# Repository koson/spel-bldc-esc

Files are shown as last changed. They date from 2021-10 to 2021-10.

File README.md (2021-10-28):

# SPEL electronic speed controller for BLDC motors 

Open-source hardware and software for BLDC motor electronic speed controller.

### About
Yet another open-source BLDC motor controller, developed primarily as a learning project. 

The end-goal is to create a controller that would be compact, flexibla and cheap to manufacture (design rules compliant with the ones from JLCPCB - 
same goes for most of the electronic components available at their SMD/SMT parts library). 

### Specification:
- Rated voltage: 60 [VDC]
- Rated current: 60 [ADC]
- Communication interfaces: CAN, I2C, UART, USB
- Debugging interface: SWD
- Control methods: through comm. interfaces, STEP/DIRECTION
- Feedback: Encoder inputs (reprogrammable to HAL sensor inputs), current sensing, back-EMF measurement. 
- CPU: STM32F103C8Tx/STM32F103CBTx series 
- Motor driver: Texas Instrument's DRV8301 
- Protection: DRV8301's built-in overcurrent/overvoltage protection modules, braking resistor.



### Hardware renders 


*SWD - IRL would be a pin header, not a socket, 3D model used for a footprint that happened to fit pin numeration accurately





### TODO: 
- BOM
- Manufacturing outlines (listing cheapest options, and possible part substitutes)
- Append calculations (somewhere)

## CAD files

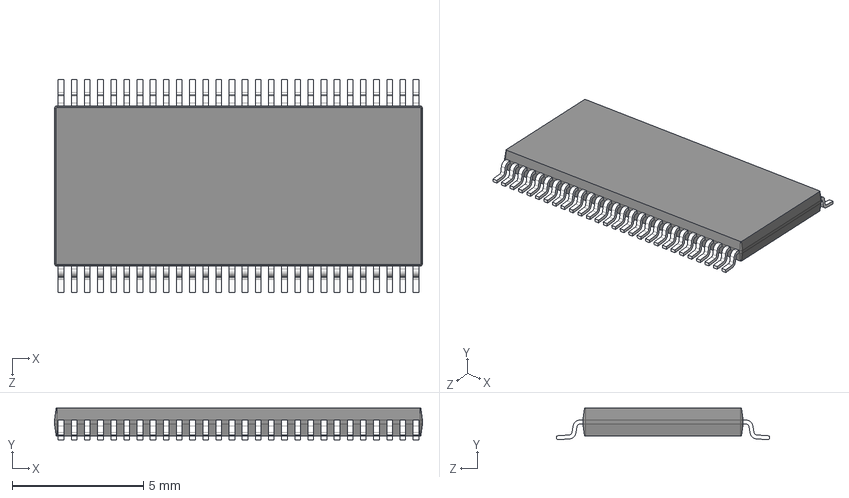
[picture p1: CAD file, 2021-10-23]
hardware/component_models/DRV8301DCAR.step
14.0 x 1.20 x 8.10 mm

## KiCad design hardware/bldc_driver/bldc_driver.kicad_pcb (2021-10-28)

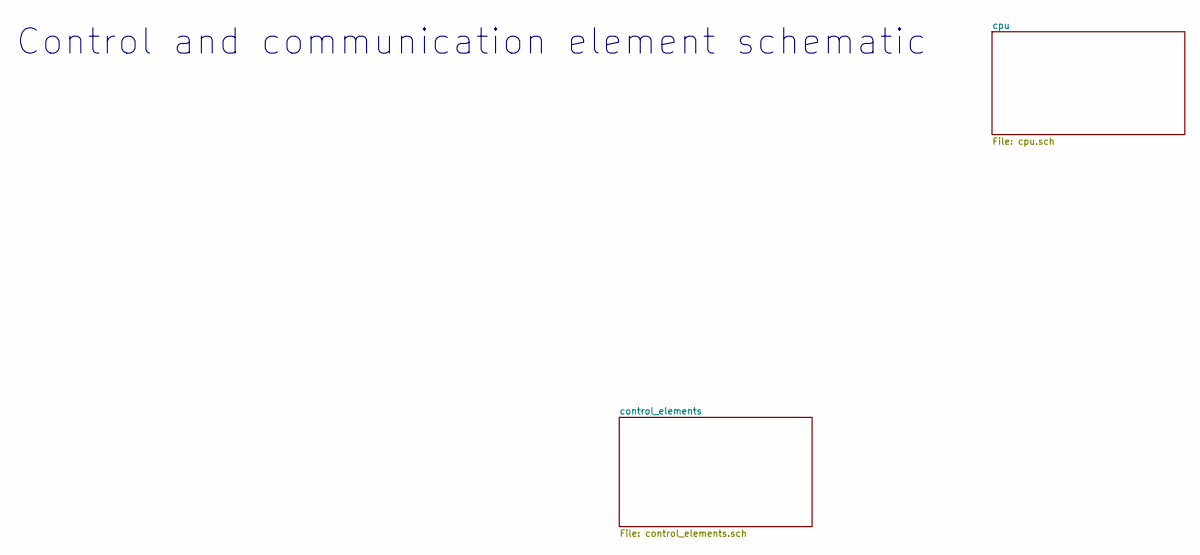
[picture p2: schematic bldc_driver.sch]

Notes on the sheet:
Control and communication element schematic

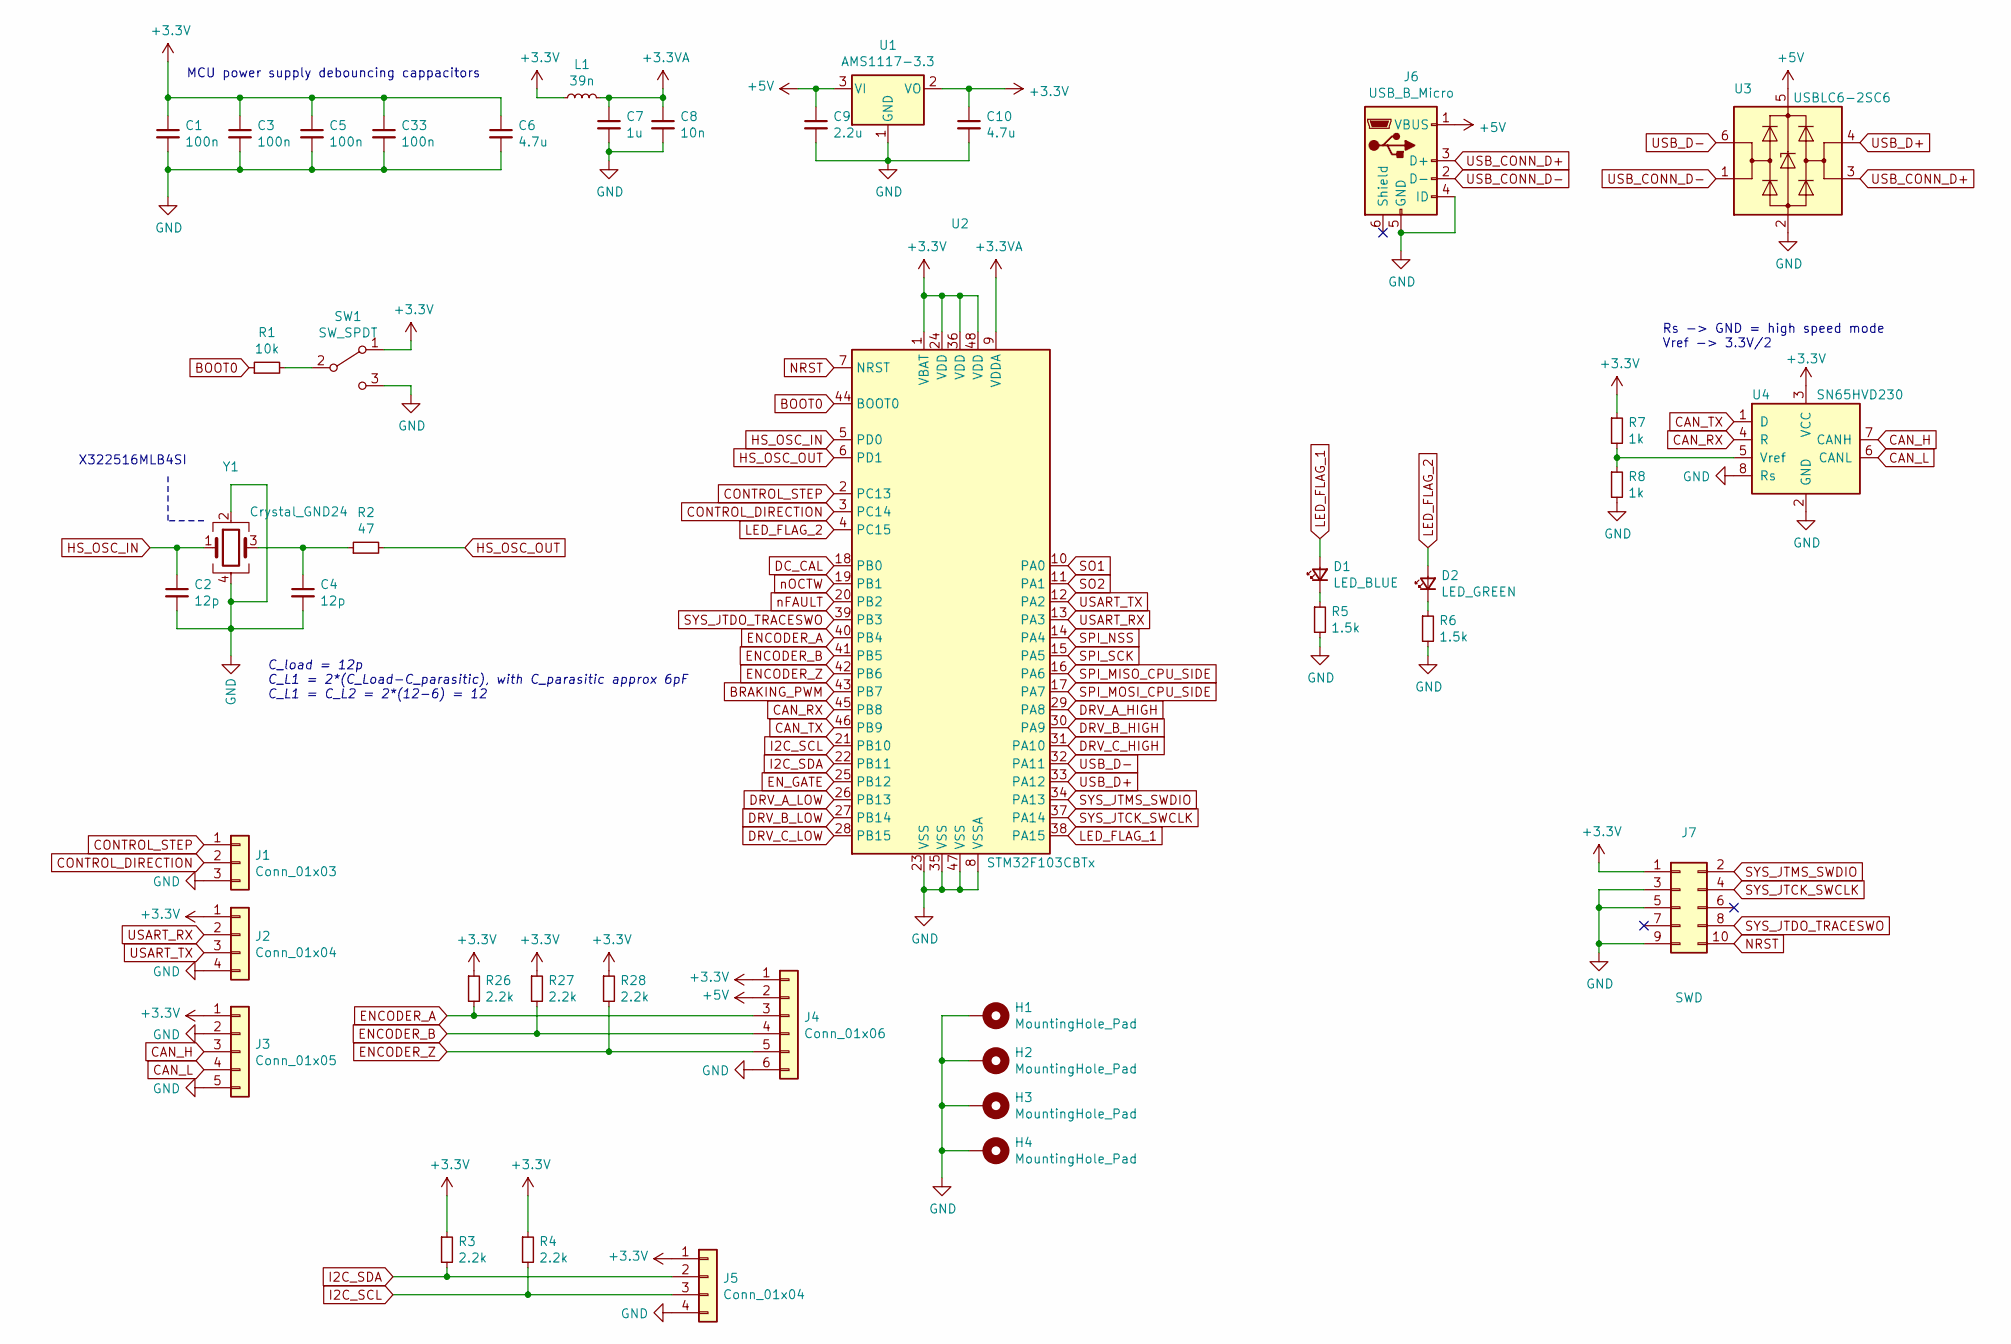
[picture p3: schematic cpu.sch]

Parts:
C1, C3, C5, C33: 100n; C_0402_1005Metric
C2, C4: 12p; C_0402_1005Metric
C6: 4.7u; C_0402_1005Metric
C7: 1u; C_0805_2012Metric
C8: 10n; C_0805_2012Metric
C9: 2.2u; C_0805_2012Metric
C10: 4.7u; C_0805_2012Metric
D1: LED_BLUE; LED_0603_1608Metric
D2: LED_GREEN; LED_0603_1608Metric
H1, H2, H3, H4: MountingHole_Pad; MountingHole_4.3mm_M4_Pad_Via
J1: Conn_01x03; PinSocket_1x03_P2.54mm_Vertical
J2, J5: Conn_01x04; PinSocket_1x04_P2.54mm_Vertical
J3: Conn_01x05; PinSocket_1x05_P2.54mm_Vertical
J4: Conn_01x06; PinSocket_1x06_P2.54mm_Vertical
J6: USB_B_Micro; USB_Micro-B_Molex_47346-0001
J7: SWD; PinSocket_2x05_P1.27mm_Vertical_SMD
L1: 39n; L_0402_1005Metric
R1: 10k; R_0402_1005Metric
R2: 47; R_0402_1005Metric
R3, R4, R26, R27, R28: 2.2k; R_0603_1608Metric
R5, R6: 1.5k; R_0603_1608Metric
R7, R8: 1k; R_0603_1608Metric
SW1: SW_SPDT; SW_SPDT_PCM12
U1: AMS1117-3.3; SOT-223-3_TabPin2
U2: STM32F103CBTx; LQFP-48_7x7mm_P0.5mm
U3: USBLC6-2SC6; SOT-23-6
U4: SN65HVD230; SOIC-8_3.9x4.9mm_P1.27mm
Y1: Crystal_GND24; Crystal_SMD_3225-4Pin_3.2x2.5mm

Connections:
+3.3VA: C7.1, C8.1, L1.2, U2.9 (VDDA); also elsewhere on the board
+3V3: C1.1, C3.1, C5.1, C6.1, C10.1, C33.1, J2.1, J3.1, J4.1, J5.1, J7.1, L1.1, R3.1, R4.1, R7.1, R26.1, R27.1, R28.1, SW1.1 (A), U1.2 (VO), U2.1 (VBAT), U2.24 (VDD), U2.36 (VDD), U2.48 (VDD), U4.3 (VCC); also elsewhere on the board
+5V: C9.1, J4.2, J6.1 (VBUS), U1.3 (VI), U3.5 (VBUS); also elsewhere on the board
-VDC: C1.2, C2.2, C3.2, C4.2, C5.2, C6.2, C7.2, C8.2, C9.2, C10.2, C33.2, H1.1, H2.1, H3.1, H4.1, J1.3, J2.4, J3.2, J3.5, J4.6, J5.4, J6.4 (ID), J6.5 (GND), J7.3, J7.5, J7.9, R5.2, R6.2, R8.2, SW1.3 (C), U1.1 (GND), U2.8 (VSSA), U2.23 (VSS), U2.35 (VSS), U2.47 (VSS), U3.2 (GND), U4.2 (GND), U4.8 (Rs), Y1.2, Y1.4; also elsewhere on the board
BOOT0: R1.1, U2.44 (BOOT0)
BRAKING_PWM: U2.43 (PB7); also elsewhere on the board
CAN_H: J3.3, U4.7 (CANH)
CAN_L: J3.4, U4.6 (CANL)
CAN_RX: U2.45 (PB8), U4.4 (R)
CAN_TX: U2.46 (PB9), U4.1 (D)
CONTROL_DIRECTION: J1.2, U2.3 (PC14)
CONTROL_STEP: J1.1, U2.2 (PC13)
DC_CAL: U2.18 (PB0); also elsewhere on the board
DRV_A_HIGH: U2.29 (PA8); also elsewhere on the board
DRV_A_LOW: U2.26 (PB13); also elsewhere on the board
DRV_B_HIGH: U2.30 (PA9); also elsewhere on the board
DRV_B_LOW: U2.27 (PB14); also elsewhere on the board
DRV_C_HIGH: U2.31 (PA10); also elsewhere on the board
DRV_C_LOW: U2.28 (PB15); also elsewhere on the board
ENCODER_A: J4.3, R26.2, U2.40 (PB4)
ENCODER_B: J4.4, R27.2, U2.41 (PB5)
ENCODER_Z: J4.5, R28.2, U2.42 (PB6)
EN_GATE: U2.25 (PB12); also elsewhere on the board
HS_OSC_IN: C2.1, U2.5 (PD0), Y1.1
HS_OSC_OUT: R2.2, U2.6 (PD1)
I2C_SCL: J5.3, R4.2, U2.21 (PB10)
I2C_SDA: J5.2, R3.2, U2.22 (PB11)
LED_FLAG_1: D1.2 (A), U2.38 (PA15)
LED_FLAG_2: D2.2 (A), U2.4 (PC15)
NRST: J7.10, U2.7 (NRST)
unnamed: C4.1, R2.1, Y1.3
unnamed: D1.1 (K), R5.1
unnamed: D2.1 (K), R6.1
unnamed: R1.2, SW1.2 (B)
unnamed: R7.2, R8.1, U4.5 (Vref)
SO1: U2.10 (PA0); also elsewhere on the board
SO2: U2.11 (PA1); also elsewhere on the board
SPI_MISO_CPU_SIDE: U2.16 (PA6); also elsewhere on the board
SPI_MOSI_CPU_SIDE: U2.17 (PA7); also elsewhere on the board
SPI_NSS: U2.14 (PA4); also elsewhere on the board
SPI_SCK: U2.15 (PA5); also elsewhere on the board
SYS_JTCK_SWCLK: J7.4, U2.37 (PA14)
SYS_JTDO_TRACESWO: J7.8, U2.39 (PB3)
SYS_JTMS_SWDIO: J7.2, U2.34 (PA13)
USART_RX: J2.2, U2.13 (PA3)
USART_TX: J2.3, U2.12 (PA2)
USB_CONN_D+: J6.3 (D+), U3.3 (I/O2)
USB_CONN_D-: J6.2 (D-), U3.1 (I/O1)
USB_D+: U2.33 (PA12), U3.4 (I/O2)
USB_D-: U2.32 (PA11), U3.6 (I/O1)
nFAULT: U2.20 (PB2); also elsewhere on the board
nOCTW: U2.19 (PB1); also elsewhere on the board

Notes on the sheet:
C_load = 12p C_L1 = 2*(C_Load-C_parasitic), with C_parasitic approx 6pF C_L1 = C_L2 = 2*(12-6) = 12
Rs -> GND = high speed mode Vref -> 3.3V/2
X322516MLB4SI
MCU power supply debouncing cappacitors

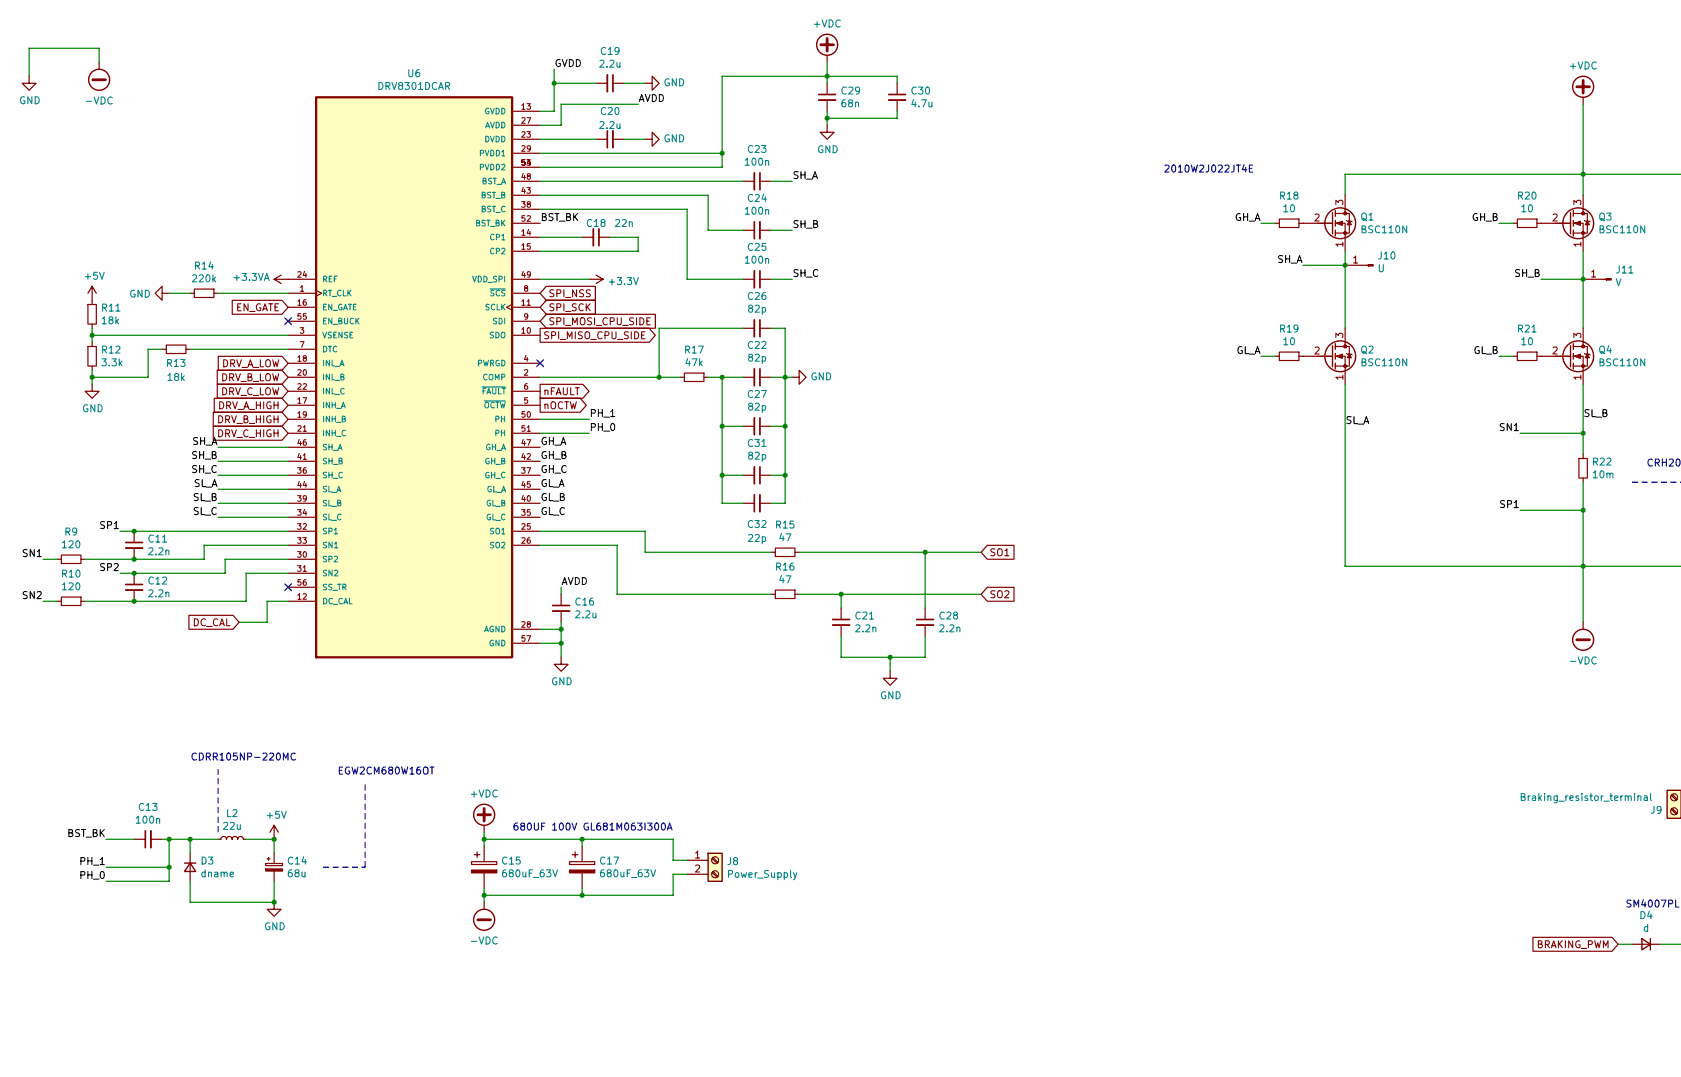
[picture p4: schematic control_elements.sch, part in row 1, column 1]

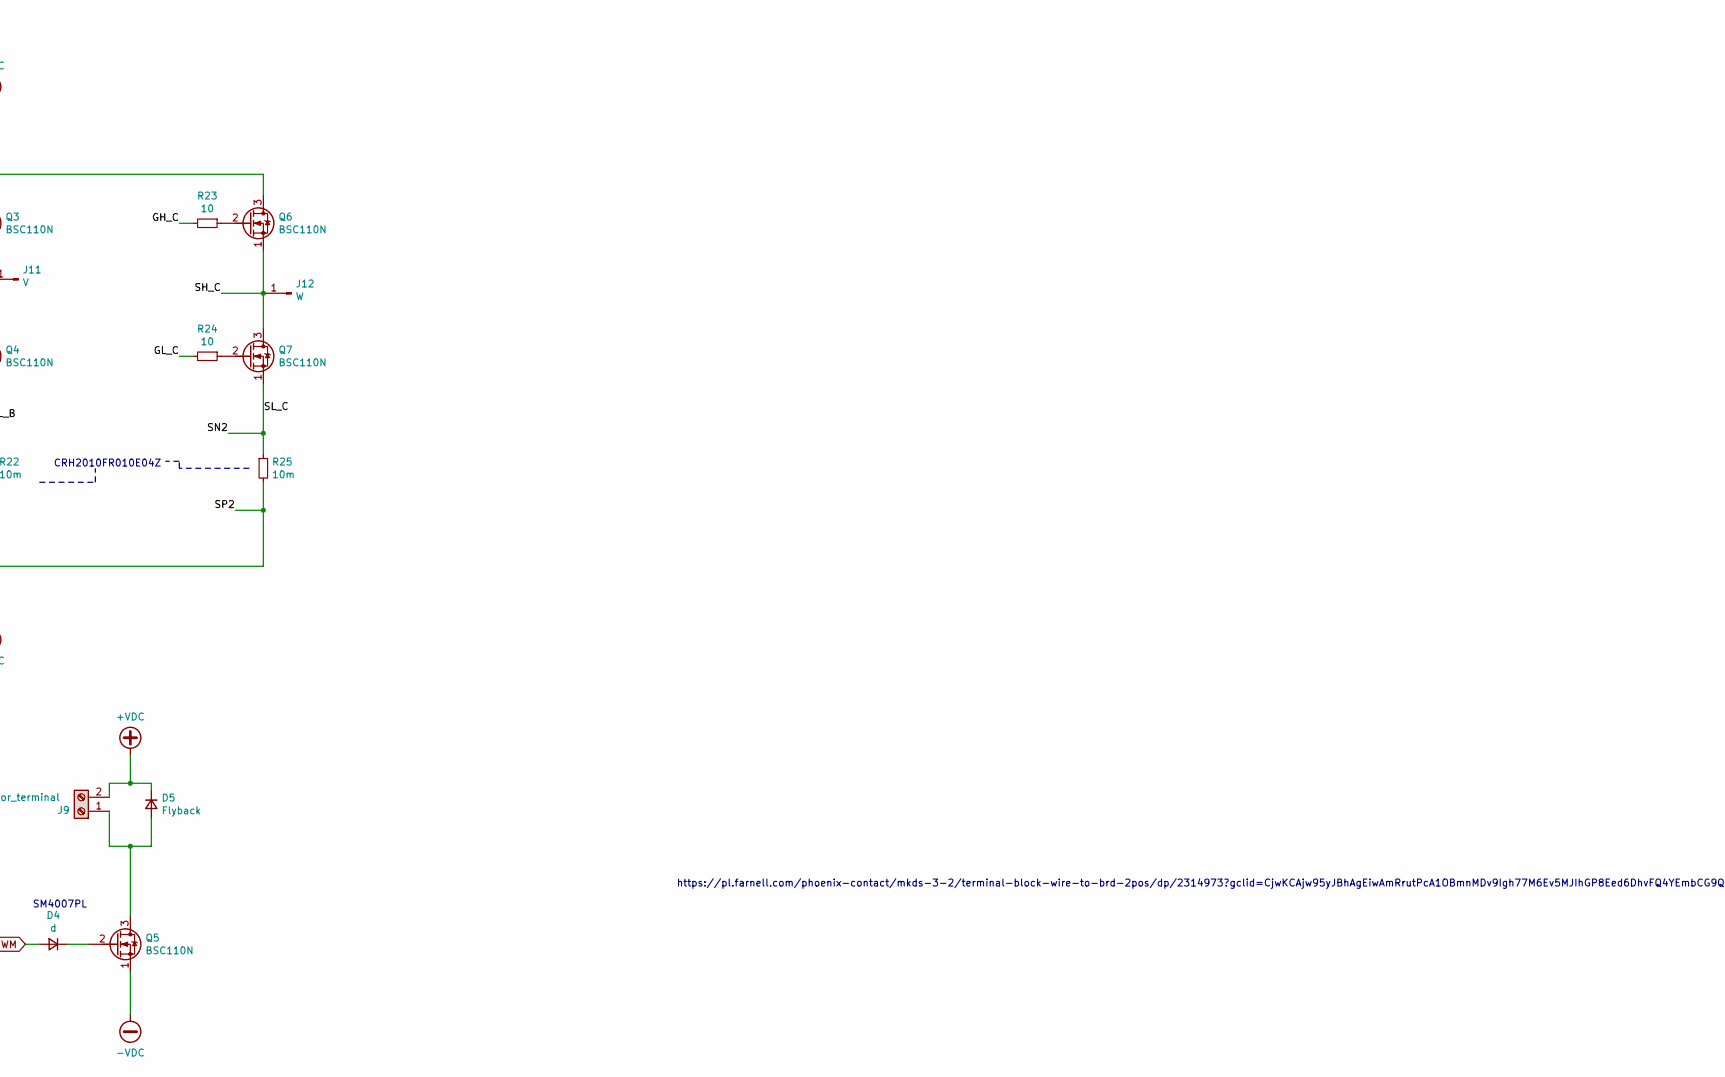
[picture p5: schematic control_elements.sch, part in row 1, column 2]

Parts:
C11, C12, C21, C28: 2.2n; C_0805_2012Metric
C13, C23, C24, C25: 100n; C_0805_2012Metric
C14: 68u; CP_Radial_D12.5mm_P5.00mm
C15, C17: 680uF_63V; CP_Radial_D13.0mm_P5.00mm
C16, C19, C20: 2.2u; C_0805_2012Metric
C18: 22n; C_0805_2012Metric
C22, C26, C27, C31: 82p; C_0603_1608Metric
C29: 68n; C_Rect_L10.0mm_W5.0mm_P5.00mm_P7.50mm
C30: 4.7u; C_1210_3225Metric
C32: 22p; C_0603_1608Metric
D3: dname; D_SOD-123F
D4: d; D_SOD-123F
D5: Flyback; D_SOD-123F
J8: Power_Supply; AMASS_XT60-F_1x02_P7.20mm_Vertical
J9: Braking_resistor_terminal; TerminalBlock_Phoenix_MKDS-3-2-5.08_1x02_P5.08mm_Horizontal
J10: U; motor_driving_pad_hole
J11: V; motor_driving_pad_hole
J12: W; motor_driving_pad_hole
L2: 22u; L_10.4x10.4_H4.8
Q1, Q2, Q3, Q4, Q5, Q6, Q7: BSC110N
R9, R10: 120; R_0805_2012Metric
R11, R13: 18k; R_0603_1608Metric
R12: 3.3k; R_0603_1608Metric
R14: 220k; R_0603_1608Metric
R15, R16: 47; R_0402_1005Metric
R17: 47k; R_0603_1608Metric
R18, R19, R20, R21, R23, R24: 10; R_0402_1005Metric
R22, R25: 10m; R_2010_5025Metric
U6: DRV8301DCAR; HTSSOP-56-1EP_6.1x14mm_P0.5mm_EP3.61x6.35mm; PARTREV F

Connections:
+3.3VA: U6.24 (REF); also elsewhere on the board
+3V3: U6.49 (VDD_SPI); also elsewhere on the board
+5V: C14.1, L2.2, R11.1; also elsewhere on the board
+VDC: C15.1, C17.1, C29.1, C30.1, D5.1 (K), J8.1, J9.2, Q1.3 (D), Q3.3 (D), Q6.3 (D), U6.29 (PVDD1), U6.53 (PVDD2), U6.54 (PVDD2)
-VDC: C11.1, C12.1, C14.2, C15.2, C16.2, C17.2, C19.1, C20.2, C21.2, C22.1, C26.1, C27.1, C28.2, C29.2, C30.2, C31.1, C32.2, D3.2 (A), J8.2, Q2.1 (S), Q5.1 (S), R12.2, R13.1, R14.2, R22.2, R25.2, U6.28 (AGND), U6.30 (SP2), U6.32 (SP1), U6.44 (SL_A), U6.57 (GND); also elsewhere on the board
/control_elements/AVDD: C16.1, U6.27 (AVDD)
/control_elements/BST_BK: C13.1, U6.52 (BST_BK)
/control_elements/GH_A: R18.2, U6.47 (GH_A)
/control_elements/GH_B: R20.2, U6.42 (GH_B)
/control_elements/GH_C: R23.2, U6.37 (GH_C)
/control_elements/GL_A: R19.2, U6.45 (GL_A)
/control_elements/GL_B: R21.2, U6.40 (GL_B)
/control_elements/GL_C: R24.2, U6.35 (GL_C)
/control_elements/GVDD: C19.2, U6.13 (GVDD)
/control_elements/PH_0: C13.2, D3.1 (K), L2.1, U6.50 (PH), U6.51 (PH)
/control_elements/SH_A: C23.1, J10.1, Q1.1 (S), Q2.3 (D), U6.46 (SH_A)
/control_elements/SH_B: C24.2, J11.1, Q3.1 (S), Q4.3 (D), U6.41 (SH_B)
/control_elements/SH_C: C25.1, J12.1, Q6.1 (S), Q7.3 (D), U6.36 (SH_C)
/control_elements/SL_B: Q4.1 (S), R9.1, R22.1, U6.39 (SL_B)
/control_elements/SL_C: Q7.1 (S), R10.2, R25.1, U6.34 (SL_C)
BRAKING_PWM: D4.2 (A); also elsewhere on the board
DC_CAL: U6.12 (DC_CAL); also elsewhere on the board
DRV_A_HIGH: U6.17 (INH_A); also elsewhere on the board
DRV_A_LOW: U6.18 (INL_A); also elsewhere on the board
DRV_B_HIGH: U6.19 (INH_B); also elsewhere on the board
DRV_B_LOW: U6.20 (INL_B); also elsewhere on the board
DRV_C_HIGH: U6.21 (INH_C); also elsewhere on the board
DRV_C_LOW: U6.22 (INL_C); also elsewhere on the board
EN_GATE: U6.16 (EN_GATE); also elsewhere on the board
unnamed: C11.2, R9.2, U6.33 (SN1)
unnamed: C12.2, R10.1, U6.31 (SN2)
unnamed: C18.1, U6.15 (CP2)
unnamed: C18.2, U6.14 (CP1)
unnamed: C20.1, U6.23 (DVDD)
unnamed: C22.2, C27.2, C31.2, C32.1, R17.1
unnamed: C23.2, U6.48 (BST_A)
unnamed: C24.1, U6.43 (BST_B)
unnamed: C25.2, U6.38 (BST_C)
unnamed: C26.2, R17.2, U6.2 (COMP)
unnamed: D4.1 (K), Q5.2 (G)
unnamed: D5.2 (A), J9.1, Q5.3 (D)
unnamed: Q1.2 (G), R18.1
unnamed: Q2.2 (G), R19.1
unnamed: Q3.2 (G), R20.1
unnamed: Q4.2 (G), R21.1
unnamed: Q6.2 (G), R23.1
unnamed: Q7.2 (G), R24.1
unnamed: R11.2, R12.1, U6.3 (VSENSE)
unnamed: R13.2, U6.7 (DTC)
unnamed: R14.1, U6.1 (RT_CLK)
unnamed: R15.1, U6.25 (SO1)
unnamed: R16.2, U6.26 (SO2)
SO1: C28.1, R15.2; also elsewhere on the board
SO2: C21.1, R16.1; also elsewhere on the board
SPI_MISO_CPU_SIDE: U6.10 (SDO); also elsewhere on the board
SPI_MOSI_CPU_SIDE: U6.9 (SDI); also elsewhere on the board
SPI_NSS: U6.8 (~SCS); also elsewhere on the board
SPI_SCK: U6.11 (SCLK); also elsewhere on the board
nFAULT: U6.6 (~FAULT); also elsewhere on the board
nOCTW: U6.5 (~OCTW); also elsewhere on the board

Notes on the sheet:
CDRR105NP-220MC
EGW2CM680W16OT
680UF 100V
GL681M063I300A
SM4007PL
CRH2010FR010E04Z
2010W2J022JT4E
https://pl.farnell.com/phoenix-contact/mkds-3-2/terminal-block-wire-to-brd-2pos/dp/2314973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|pcrid|459816541164|plid||kword||match||slid||product|2314973|pgrid|114468574544|ptaid|pla-32…

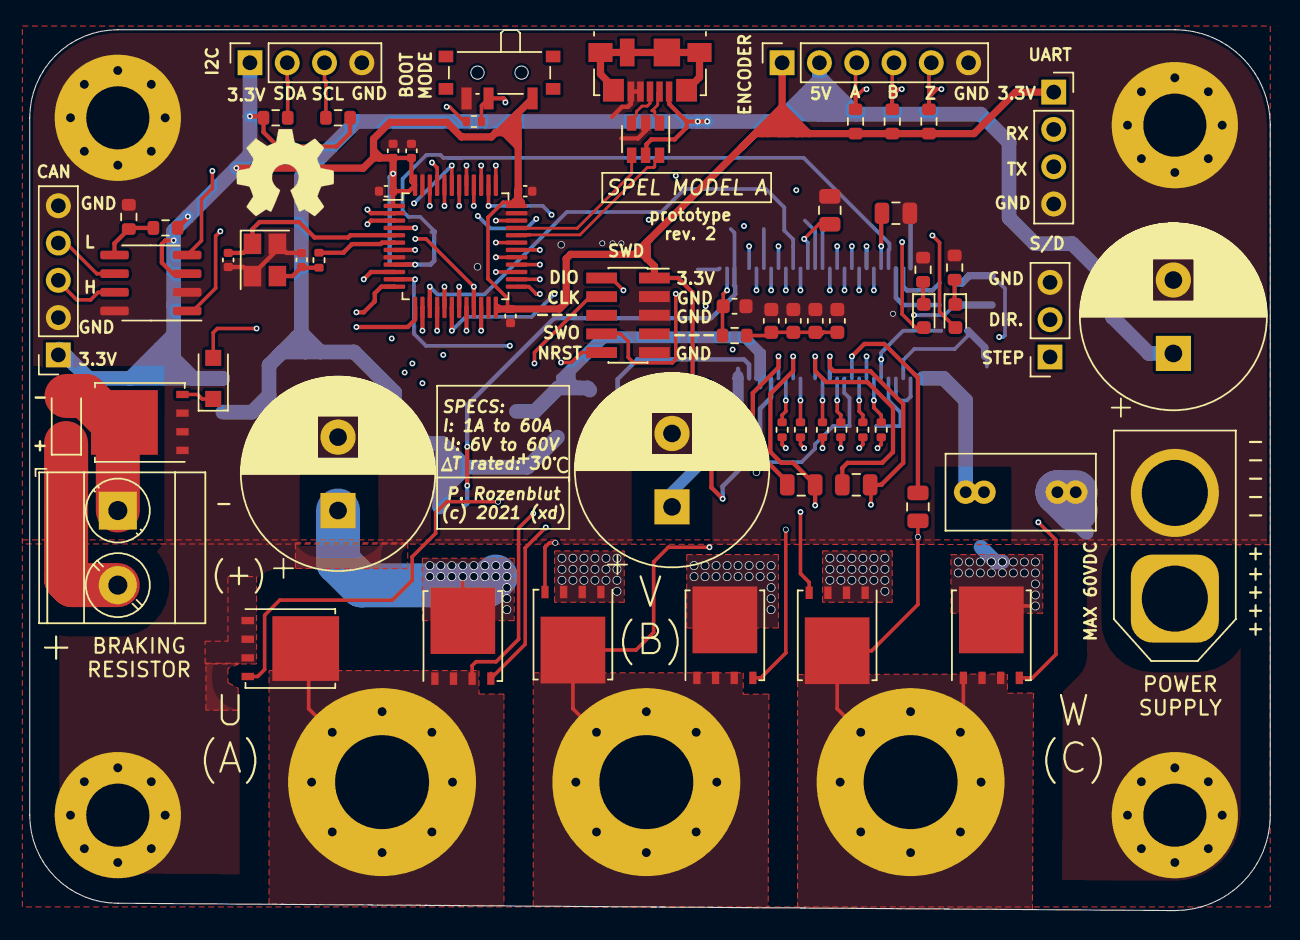
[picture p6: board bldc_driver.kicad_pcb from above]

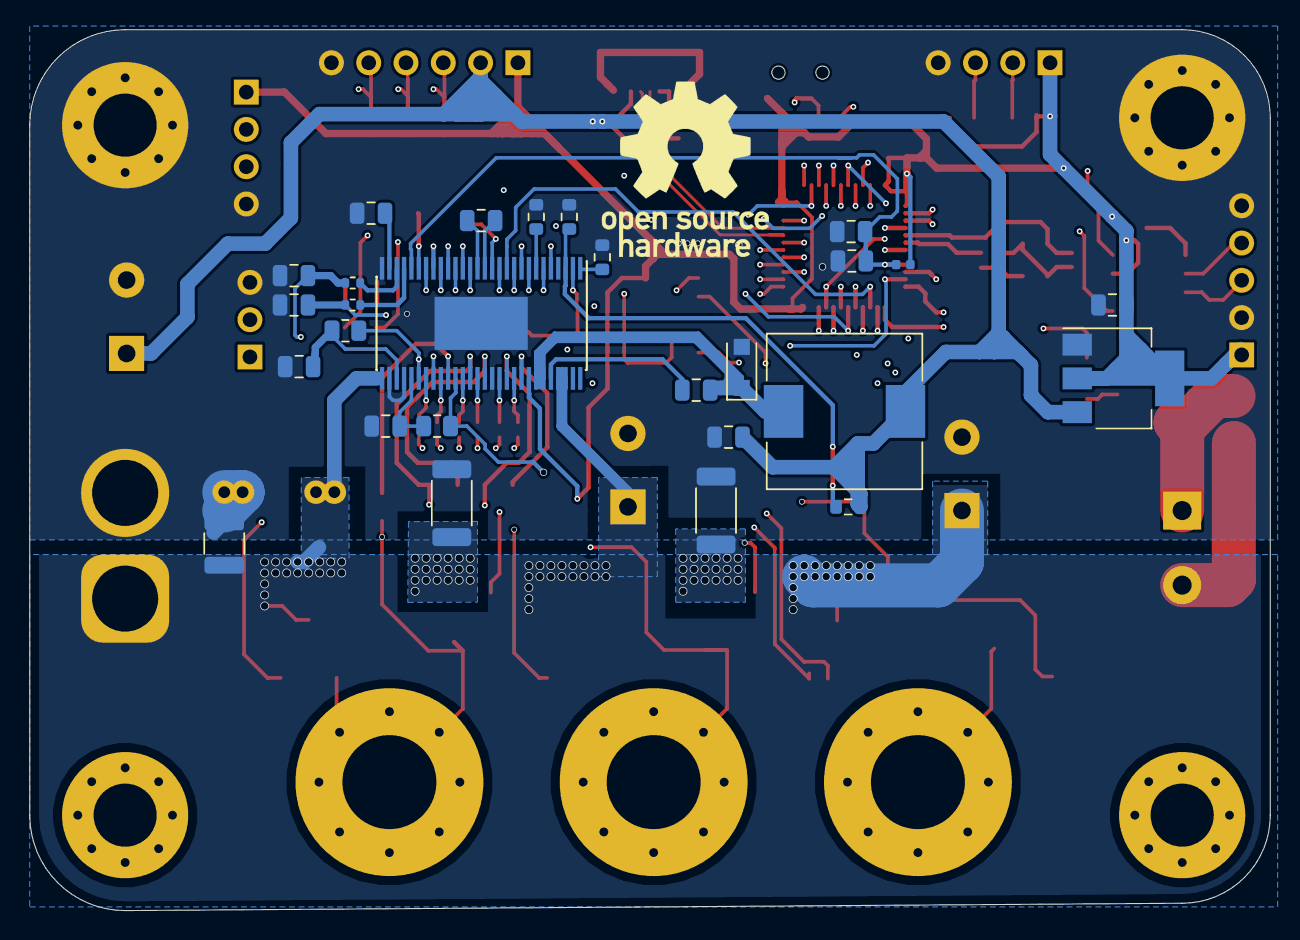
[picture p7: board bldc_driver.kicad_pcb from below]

Board: 4 copper layers, 84.5 x 60.0 mm, 98 parts (27 on the bottom side), 91 nets.

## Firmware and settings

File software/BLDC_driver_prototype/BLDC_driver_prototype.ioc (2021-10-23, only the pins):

Mcu.UserName=STM32F103CBTx
PA0-WKUP.GPIO_Label=SO1
PA0-WKUP.Signal=ADCx_IN0
PA1.GPIO_Label=SO2
PA1.Signal=ADCx_IN1
PA10.Signal=S_TIM1_CH3
PA11.Signal=USB_DM
PA12.Signal=USB_DP
PA13.Signal=SYS_JTMS-SWDIO
PA14.Signal=SYS_JTCK-SWCLK
PA15.GPIO_Label=LED_FLAG_1
PA15.Signal=GPIO_Output
PA2.Signal=USART2_TX
PA3.Signal=USART2_RX
PA4.Signal=SPI1_NSS
PA5.Signal=SPI1_SCK
PA6.Signal=SPI1_MISO
PA7.Signal=SPI1_MOSI
PA8.Signal=S_TIM1_CH1
PA9.Signal=S_TIM1_CH2
PB0.GPIO_Label=DC_CAL
PB0.Signal=GPIO_Output
PB1.GPIO_Label=nOCTW
PB1.Signal=GPXTI1
PB10.Signal=I2C2_SCL
PB11.Signal=I2C2_SDA
PB12.GPIO_Label=EN_GATE
PB12.Signal=GPIO_Output
PB13.Signal=TIM1_CH1N
PB14.Signal=TIM1_CH2N
PB15.Signal=TIM1_CH3N
PB2.GPIO_Label=nFAULT
PB2.Signal=GPXTI2
PB3.Signal=SYS_JTDO-TRACESWO
PB4.GPIO_Label=ENCODER_A
PB4.Signal=GPXTI4
PB5.GPIO_Label=ENCODER_B
PB5.Signal=GPXTI5
PB6.GPIO_Label=ENCODER_Z
PB6.Signal=GPXTI6
PB7.GPIO_Label=BRAKING_PWM
PB7.Signal=S_TIM4_CH2
PB8.Signal=CAN_RX
PB9.Signal=CAN_TX
PC13-TAMPER-RTC.GPIO_Label=CONTROL_STEP
PC13-TAMPER-RTC.Signal=GPXTI13
PC14-OSC32_IN.GPIO_Label=CONTROL_DIRECTION
PC14-OSC32_IN.Signal=GPIO_Input
PC15-OSC32_OUT.GPIO_Label=LED_FLAG_2
PC15-OSC32_OUT.Signal=GPIO_Output
PD0-OSC_IN.Signal=RCC_OSC_IN
PD1-OSC_OUT.Signal=RCC_OSC_OUT

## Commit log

2021-10-23 init
    - Pushed all the project files from the second project revision
    [DRV8301DCAR.step, bldc_driver.kicad_pcb, bldc_driver.sch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]
2021-10-23 init software files
    - added STM32 configuration file
2021-10-23 Create README.md
    - forgot about the braking resistor
2021-10-23 added OSHW logos
    [bldc_driver.kicad_pcb]
2021-10-28 Cosmetic - trace improvements
    - correcting 3-way trace intersections
    [bldc_driver.kicad_pcb, bldc_driver.sch, control_elements.sch]
2021-10-28 Cosmetics
    -> Trace corrections cont'd
    [bldc_driver.kicad_pcb]

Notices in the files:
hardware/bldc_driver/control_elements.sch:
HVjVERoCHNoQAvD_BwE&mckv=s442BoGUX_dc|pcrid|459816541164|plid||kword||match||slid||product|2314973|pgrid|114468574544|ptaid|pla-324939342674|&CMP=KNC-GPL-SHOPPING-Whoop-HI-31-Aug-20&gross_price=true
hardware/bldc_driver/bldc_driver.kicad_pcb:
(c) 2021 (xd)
